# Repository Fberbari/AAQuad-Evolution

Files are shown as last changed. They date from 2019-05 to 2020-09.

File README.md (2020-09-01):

# AAQuad-Evolution
---

The AAQuad-Evolution is a flight computer I've designed to control a quadcopter. The computer takes care of continued stabilization in flight while leaving the pilot free to command roll, pitch, and yaw angles as well as altitude. The project is made up of a custom PCB, all the bare-metal C code that runs on the Atmega328pb processor and Matlab simulations used to design and tune the PID algorithms. This is very much a bare bones flight computer that is in no way as feature rich as BetaFlight or any of the other famous FOS flight controllers. Its advantage lies in its simplicity. Anyone with some understanding of the dynamics of flight, calculus, and circuitry could begin to understand the project without being faced with a mountain of complexity and no idea where to start. In the end, the AAQuad-Evolution continues to satisfy my curiosity for flight and increase my understanding of embedded systems all the while providing me with a creative outlet to try out all kinds of cool things.



## Flying the Quad
---

The commands are as such:

* Increasing/decreasing the throttle stick corresponds to an increase/decrease in the target altitude.
* Increasing/decreasing the rudder stick corresponds to an increase/decrease in the target azimuth (relative to the starting azimuth).
* Increasing/decreasing the aileron stick corresponds to an increase/decrease in the target bank angle.
* Increasing/decreasing the elevator stick corresponds to an increase/decrease in the target pitch angle.

The ranges for all the mentioned targets are defined in src/Pid.h.

## Calibrating the Quad
---

1. Before plugging in the battery, turn the transmitter on and put the throttle stick to full power.
2. Plug in the battery.
	* A solid green led will turn on, indicating calibration mode has been successfully entered.
3. Position the Quad on a level surface and make sure it is completely still.
4. Put the throttle stick to 0.
	* The led will turn off, indicating calibration has begun.
5. Once the led turns on again, the Quad has been successfully calibrated and is ready to be flown.

### Some in flight images

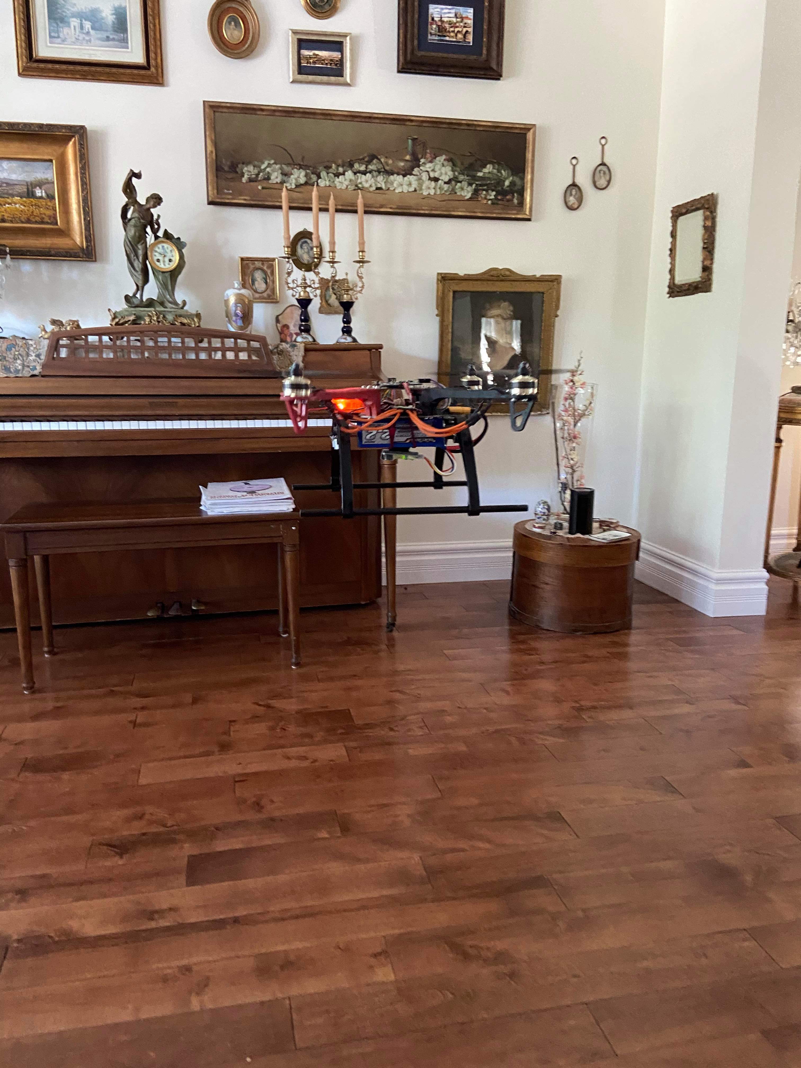
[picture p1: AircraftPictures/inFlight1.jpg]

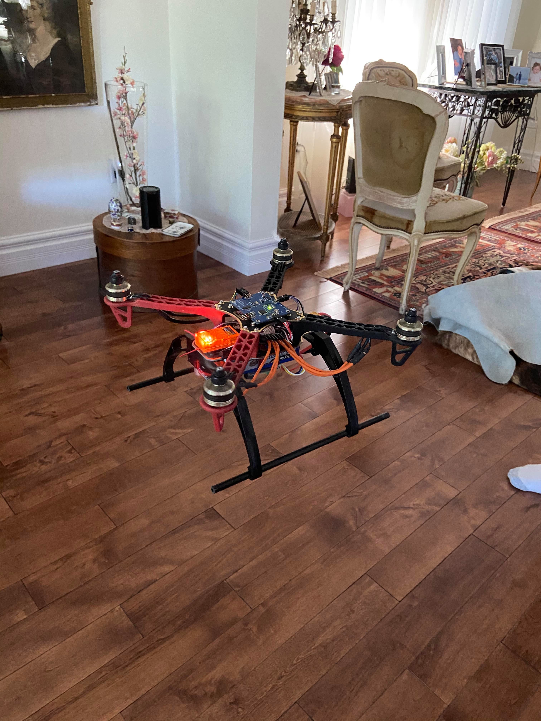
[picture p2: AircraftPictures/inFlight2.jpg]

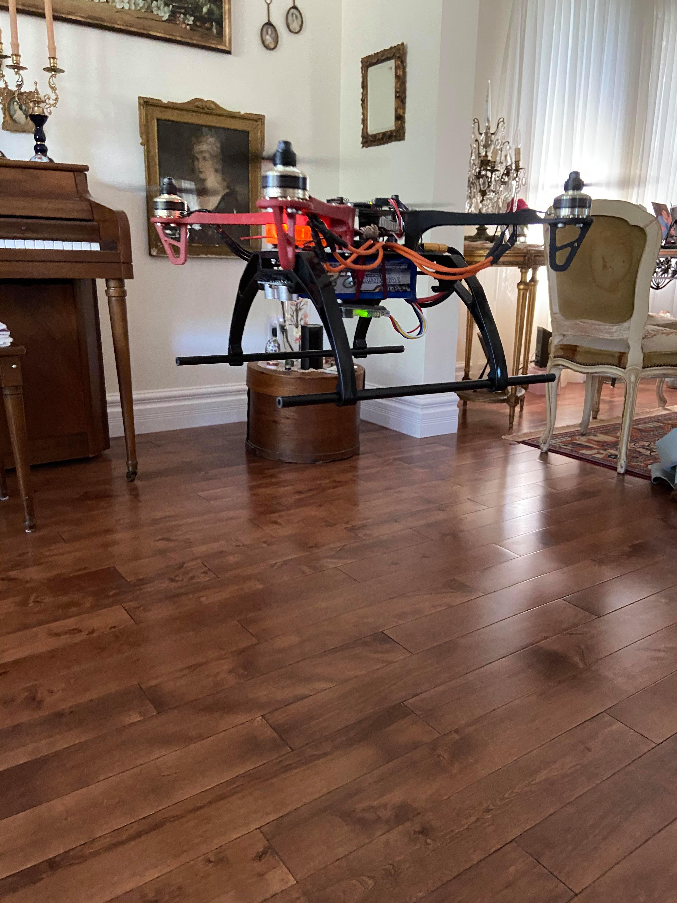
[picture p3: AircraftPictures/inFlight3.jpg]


### Some close ups

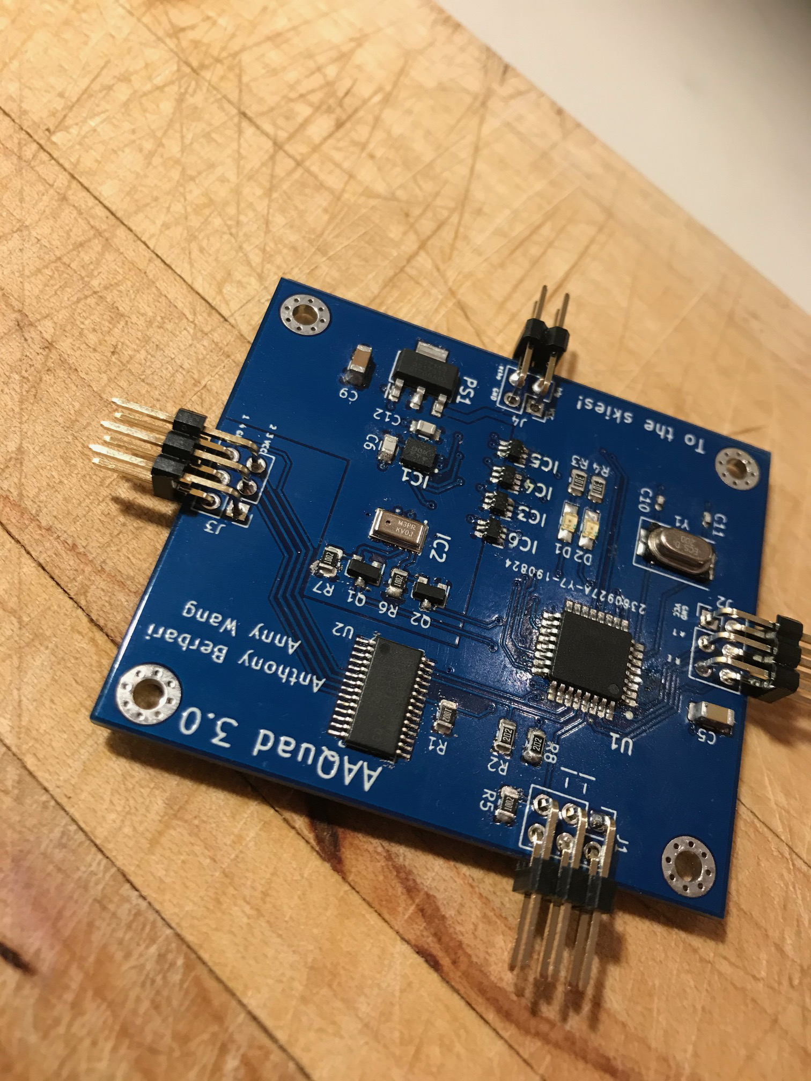
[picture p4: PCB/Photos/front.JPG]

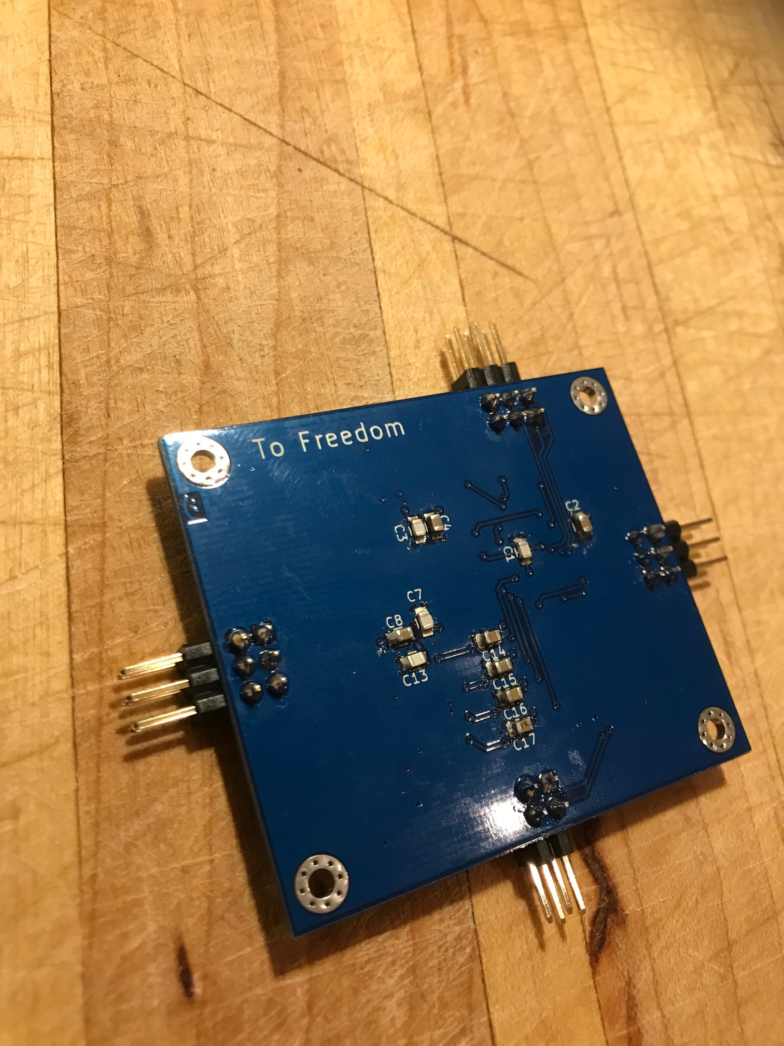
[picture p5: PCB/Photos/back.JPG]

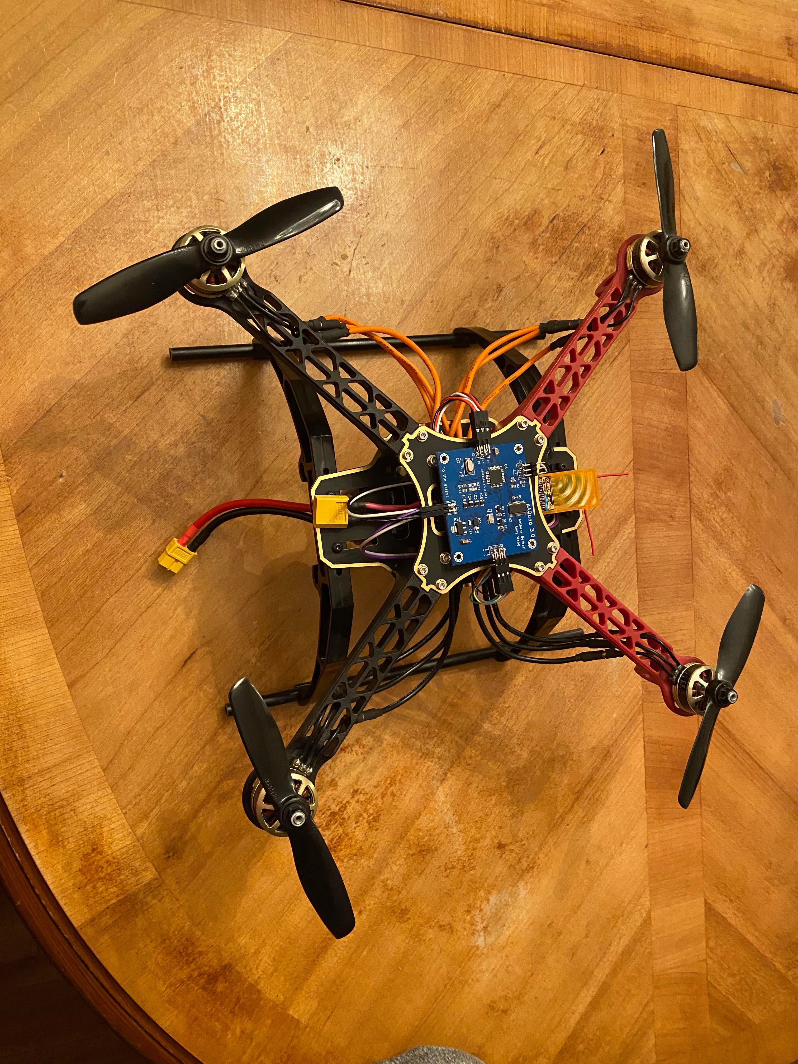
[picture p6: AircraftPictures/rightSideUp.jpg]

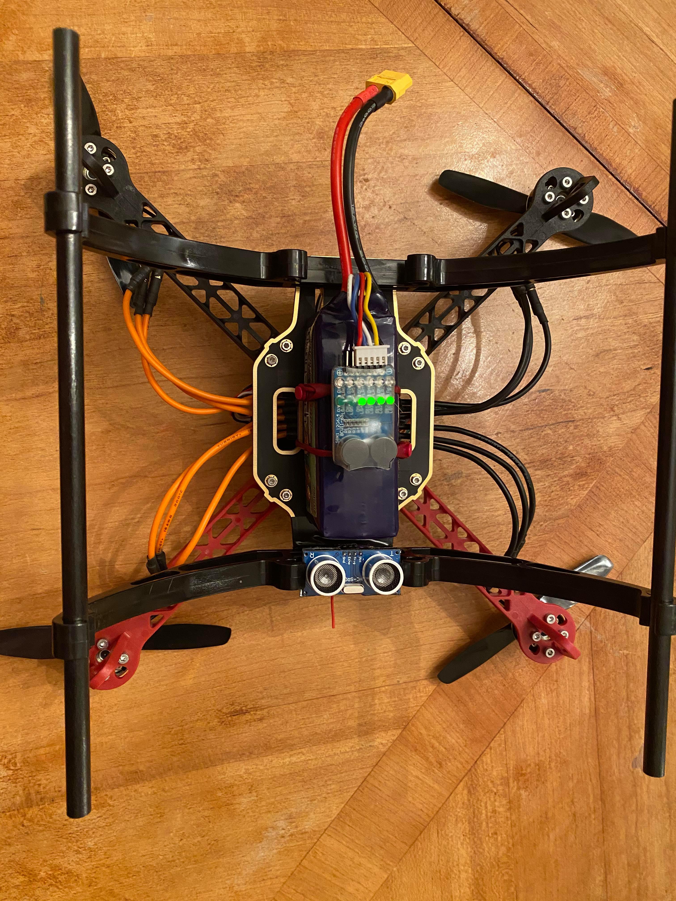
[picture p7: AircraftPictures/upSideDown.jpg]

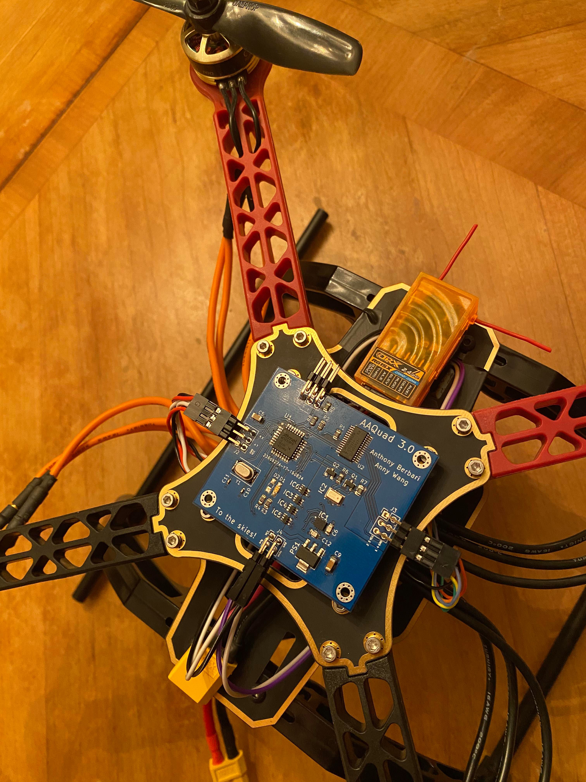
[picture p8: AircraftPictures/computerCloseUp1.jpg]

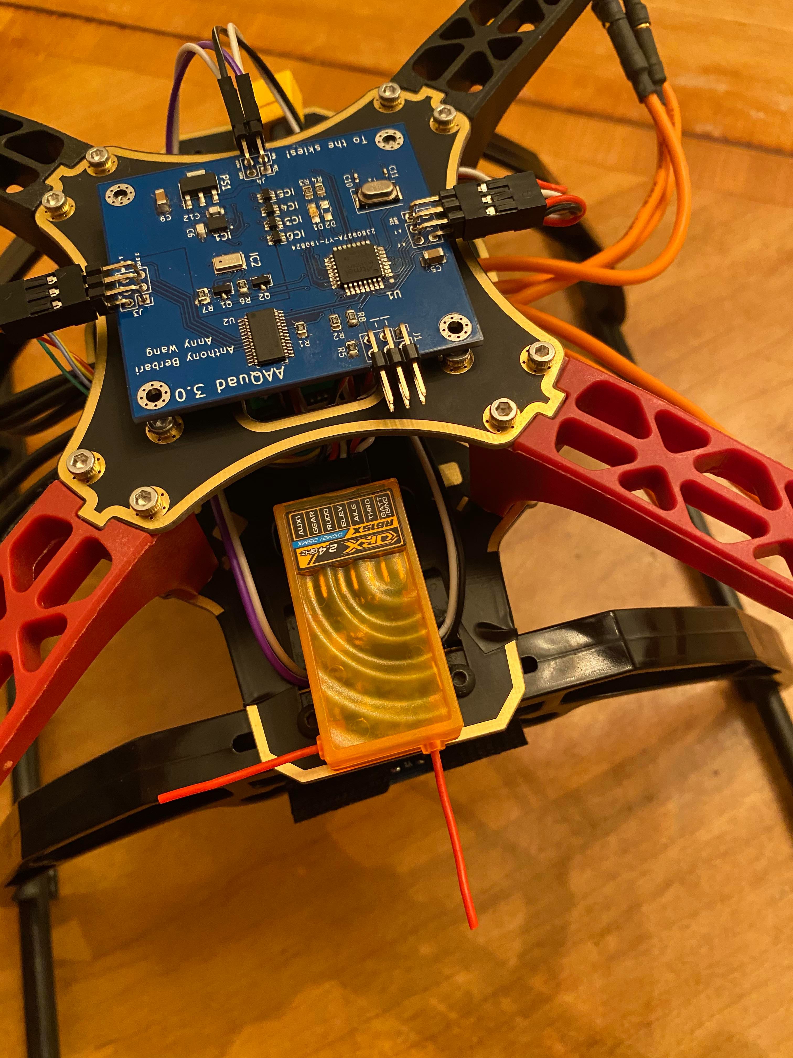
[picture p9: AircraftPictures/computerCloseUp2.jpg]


## What's going on ?
---

So you want to understand how the AAQuad flies ? Great! Here is a high level explanation of what's going on.

Everything starts in main.c, which you'll find in the root directory of the project. If you go through that file, you'll find it's incredibly simple in principle. Here, we begin with a short delay to ensure all electrical systems have stabilized after power up. Next, we execute a calibration and finally, we call the controller state machine inside an infinite loop (this is where the magic happens).

Now, let's head into the src directory. Apart from main.c, this is where all the the source and header files are stored. Take a look at the state machine in Controller.c (the switch case statement inside the Controller_DoYourThingAndFlyTheQuadITrustYou function). The switch statement is organized in the order that the states get executed. Here's what's going on:

1. GetPilotInstructions: We check to see whether there are any new instructions from the receiver. If you take a look inside the PilotInstructions module, you'll see that the pwm signals sent from the ESC are read asynchronously via external and pin change interrupts. Those instructions get translated into percentages for commanded roll, pitch, yaw and altitude. If they are ready when PilotInstructions_ComputePilotResult is called, we pick them up. Otherwise, we just move on and pick them up the next time.

2. GetImuData: We collect the accelerometer, gyroscope and magnetometer data from the inertial measurement unit. This is also an interrupt based exchanged so when we call Imu_GetResult, we are just checking if the data is ready and picking it up if it is.

3. GetAltitude: We collect data from the ultrasonic distance sensor. Once again, it is an interrupt based exchange, so we are just checking and picking data up if it is ready.

4. TriggerNewMeasurements: Now that we've collected all the data of interest, we need to instruct the sensors to collect more data for us. This way, when the time comes once again to ask for it, it will be ready. For the IMU, this triggers an interrupt based SPI exchange that reads the registers that contain the relevant data. For the ultrasonic distance sensor, this sends the digital pulse instructing it to collect a new measurement.

5. FuseMeasurements: While the sensors do their thing, we begin to crunch the math. In this state, we fuse gyroscope and accelerometer data together using a Mahony filter. This filter returns the estimated orientation of the quad encoded in a quaternion.

6. ConvertToEuler: Since quaternions are very non linear and thus hard to use in a linear controller, we convert them into Euler angles. These are the familiar roll, pitch and yaw angles. At the same time, we also compute the derivatives of the Euler angles (representative of the angular velocity of the quad in every axis). This is for future use in the controller. It is done this way because computing a derivative from the change in measured angular positions leaves us very susceptible to noise. Since we have a gyroscope and measure the derivatives directly, we can use those values and avoid this problem.

7. ComputePid: Now that we know what the pilot wants and what the quad is doing, we can compute what we need the motors to do to achieve the pilot's intentions. This is done via multiple PID (proportional, integral, derivative) algorithms. This module also takes care of figuring out the takeoff sequence of the quad. What we get from it is an array of 4 floats that correspond to percentages of full power that need to be delivered to each motor to achieve the desired intentions.

8. SendToPwm: Once we know what we want the motors to do, we need to communicate that to them. To do so, we begin an interrupt based I2C exchange with a chip responsible for sending out PWM to the ESC.

9. WaitForTimer: Last, to keep things synchronous, we sit in this state until a timer says some set time has passed. Once that is the case, we go back to the GetPilotInstructions state and the cycle begins anew.

10. Failed: This state should never be reached in normal flight but exists in case a catastrophic failure needs to be handled. In the case that something goes horribly wrong in one of the modules (for example communication gets cut with one of our chips), we go to this state and the PWM output to the ESC gets immediately shutdown, causing the motors to stop spinning.

## Building it for yourself
---

A word of caution. This project was not designed to be reproduced, so it is fairly difficult to do so. That being said, if anyone does want to construct the PCB and tune then upload the software, here is what they would need to do:

### Prereq Hardware

* [Avr-Ice Jtag programmer](https://www.digikey.ca/en/product-highlight/a/atmel/atmel-ice-programmer-debugger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)
* A 4 channel ESC with 5V BEC that can handle 200 Hz PWM refresh rates
* A minimum 4 channel receiver that communicates over PWM
* Your favorite quadcopter frame, motors, and battery
* A transmitter capable of communicating with your esc of choice

### Prereq Software

* Atmel studio 7+
* Kicad 5+ (Optional, as the gerbers are already in the repo)
* Simulink 2019+, equipped with the aerospace blockset

### Building the PCB

Full gerber files and a BOM are present in the PCB/KicadFiles directory.
The only sensor not present in the BOM is the [ultrasonic distance sensor](https://www.sparkfun.com/products/15569).
You will also need to purchase the appropriate wires to connect the ESC, receiver, and ultrasonic sensor to the PCB.

### Adjusting the PID gains

If you know the mass, inertia tensor, and relationship between throttle percentage, force and torque of your quadcopter, you can adjust the appropriate blocks in the Simulink model and tune the PID gains. You can insert those gains into src/Pid.c.

### Compiling and uploading the software

Once the pcb is built, power it by connecting the ESC to the battery and plug in the Jtag programmer to the appropriate pins. To open the project in Atmel studio, open the project file present in /build. Then, click the compile button and the run button.

## License

This project is under the MIT license.

## Acknowledgements

* SOH Madgwick, whose implementation of the Mahony filter is used in this project.
* A shoutout to Anny Wang, who said: "Hey, wouldn't it be cool to build a quadcopter ?" back in 2018, which is how this project began :p.

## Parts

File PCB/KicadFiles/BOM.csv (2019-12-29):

value | footprint | libsource/_lib | libsource/_part | libsource/_description | sheetpath/_names | sheetpath/_tstamps | tstamp | _ref | datasheet | fields/field/0/_name | fields/field/0/__text | fields/field/1/_name | fields/field/1/__text | fields/field/2/_name | fields/field/2/__text | fields/field/3/_name | fields/field/3/__text | fields/field/4/_name | fields/field/4/__text | fields/field/5/_name | fields/field/5/__text | fields/field/6/_name | fields/field/6/__text | fields/field/7/_name | fields/field/7/__text | fields/field/8/_name | fields/field/8/__text
programmer | Connector_PinHeader_2.54mm:PinHeader_2x03_P2.54mm_Vertical | AAquad_PCB-rescue | Conn_02x03_Counter_Clockwise |  | / | / | 5AFFD18C | J1
10K | Resistor_SMD:R_0805_2012Metric | AAquad_PCB-rescue | R |  | / | / | 5B009C4D | R6
0.1uF | Capacitors_SMD:C_0805 | AAquad_PCB-rescue | C |  | / | / | 5B01389E | C7
10uF | Capacitors_SMD:C_0805 | AAquad_PCB-rescue | C |  | / | / | 5B01393C | C8
green | LEDs:LED_0805_HandSoldering | AAquad_PCB-rescue | LED |  | / | / | 5B01445F | D1
0.1uF | Capacitors_SMD:C_0805 | AAquad_PCB-rescue | C |  | / | / | 5B01AE0E | C3
10uF | Capacitors_SMD:C_0805 | AAquad_PCB-rescue | C |  | / | / | 5B01AECE | C4
0.1uF | Capacitors_SMD:C_0805 | AAquad_PCB-rescue | C |  | / | / | 5B01F518 | C1
10uF | Capacitors_SMD:C_0805 | AAquad_PCB-rescue | C |  | / | / | 5B01F5DD | C2
10K | Resistor_SMD:R_0805_2012Metric | AAquad_PCB-rescue | R |  | / | / | 5B020FB2 | R5
300 | Resistor_SMD:R_0805_2012Metric | AAquad_PCB-rescue | R |  | / | / | 5B014D38 | R3
BSS138 | TO_SOT_Packages_SMD:SOT-23 | AAquad_PCB-rescue | BSS138 |  | / | / | 5B066D86 | Q2
BSS138 | TO_SOT_Packages_SMD:SOT-23 | AAquad_PCB-rescue | BSS138 |  | / | / | 5B0670F5 | Q1
SPX1117M3-L-5-0_TR | SamacSys_Parts:SOT230P700X170-4N | AAquad_PCB-rescue | SPX1117M3-L-5-0_TR |  | / | / | 5B6A5D1A | PS1 | https://www.exar.com/ds/spx1117_ds_r210_082411.pdf | Arrow Part Number | SPX1117M3-L-5-0/TR | Arrow Price/Stock | https://www.arrow.com/en/products/spx1117m3-l-5-0tr/exar | Description | LDO Voltage Regulators 800mALOW DROPOUT | Height | 1.7 | Manufacturer_Name | EXAR | Manufacturer_Part_Number | SPX1117M3-L-5-0/TR
MPL3115A2 | sensors:MPL3115A2 | MPL3115A2 | MPL3115A2 | MPL3115A2, Absolute Pressure Sensor, 110kPa 0.9 1 V Output, 8-Pin LGA | / | / | 5D61CB39 | IC2 | http://uk.rs-online.com/web/p/products/7500841 | Description | MPL3115A2, Absolute Pressure Sensor, 110kPa 0.9 1 V Output, 8-Pin LGA | Manufacturer_Name | Nexperia | Manufacturer_Part_Number | MPL3115A2 | RS Part Number | 7500841 | RS Price/Stock | http://uk.rs-online.com/web/p/products/7500841
0.1uF | Capacitors_SMD:C_0805 | Device | C | Unpolarized capacitor | / | / | 5D72BD62 | C13 | ~
100uF | Capacitor_SMD:C_1206_3216Metric | Device | C | Unpolarized capacitor | / | / | 5DA2FA31 | C9 | ~
BMX160 | sensors:bmx160 | BMX160 | BMX160 | IMUs - Inertial Measurement Units 9-axis (9DOF) Absolute Orientation MEMS Sensor | / | / | 5DA63717 | IC1 | http://www.mouser.com/datasheet/2/783/BST-BMX160-DS000-11-1480547.pdf | Description | IMUs - Inertial Measurement Units 9-axis (9DOF) Absolute Orientation MEMS Sensor | Height | 0.88 | Manufacturer_Name | Bosch Sensortec | Manufacturer_Part_Number | BMX160 | Mouser Part Number | 262-BMX160 | Mouser Price/Stock | https://www.mouser.com/Search/Refine.aspx?Keyword=262-BMX160
10K | Resistor_SMD:R_0805_2012Metric | Device | R | Resistor | / | / | 5DCD5F56 | R1 | ~
PCA9685PW_112 | digikey-footprints:TSSOP-28_W4.40mm | AAquad_PCB-rescue | PCA9685PW_112-RESCUE-AAquad_PCB |  | / | / | 5B007CE9 | U2 | https://www.nxp.com/docs/en/data-sheet/PCA9685.pdf | Category | Integrated Circuits (ICs) | DK_Datasheet_Link | https://www.nxp.com/docs/en/data-sheet/PCA9685.pdf | DK_Detail_Page | /product-detail/en/nxp-usa-inc/PCA9685PW,112/568-8366-5-ND/2034324 | Description | IC LED DRVR LIN DIM 25MA 28TSSOP | Digi-Key_PN | 568-8366-5-ND | Family | PMIC - LED Drivers | MPN | PCA9685PW,112 | Manufacturer | NXP USA Inc. | Status | Active
2K | Resistor_SMD:R_0805_2012Metric | Device | R | Resistor | / | / | 5DE25B41 | R8 | ~
2K | Resistor_SMD:R_0805_2012Metric | Device | R | Resistor | / | / | 5DE26598 | R2 | ~
Atmega328pb | microcontrollers:ATMEGA328PB-ANR | Misc | Atmega328pb |  | / | / | 5D60BAF7 | U1
10K | Resistor_SMD:R_0805_2012Metric | AAquad_PCB-rescue | R |  | / | / | 5B009BD8 | R7
Crystal | Crystals:Crystal_SMD_7050-2pin_7.0x5.0mm | Device | Crystal | Two pin crystal | / | / | 5D83D52A | Y1 | ~
33pF | Capacitor_SMD:C_0402_1005Metric | Device | C | Unpolarized capacitor | / | / | 5D880116 | C11 | ~
33pF | Capacitor_SMD:C_0402_1005Metric | Device | C | Unpolarized capacitor | / | / | 5D88142F | C10 | ~
Receiver_Output | Connector_PinHeader_2.54mm:PinHeader_2x03_P2.54mm_Vertical | Connector_Generic | Conn_02x03_Counter_Clockwise | Generic connector, double row, 02x03, counter clockwise pin numbering scheme (similar to DIP packge numbering), script generated (kicad-library-utils/schlib/autogen/connector/) | / | / | 5D8ADF89 | J2 | ~
ESC_Input | Connector_PinHeader_2.54mm:PinHeader_2x03_P2.54mm_Vertical | Connector_Generic | Conn_02x03_Counter_Clockwise | Generic connector, double row, 02x03, counter clockwise pin numbering scheme (similar to DIP packge numbering), script generated (kicad-library-utils/schlib/autogen/connector/) | / | / | 5D8AF12E | J3 | ~
100uF | Capacitor_SMD:C_1206_3216Metric | Device | C | Unpolarized capacitor | / | / | 5D990D4F | C5 | ~
0.1uF | Capacitors_SMD:C_0805 | Device | C | Unpolarized capacitor | / | / | 5D9AE831 | C6 | ~
0.1uF | Capacitors_SMD:C_0805 | Device | C | Unpolarized capacitor | / | / | 5D9BB021 | C12 | ~
300 | Resistor_SMD:R_0805_2012Metric | AAquad_PCB-rescue | R |  | / | / | 5B014C86 | R4
red | LEDs:LED_0805_HandSoldering | AAquad_PCB-rescue | LED |  | / | / | 5B014543 | D2
ultrasonic | Connector_PinHeader_2.54mm:PinHeader_2x02_P2.54mm_Vertical | Connector_Generic | Conn_02x02_Counter_Clockwise | Generic connector, double row, 02x02, counter clockwise pin numbering scheme (similar to DIP packge numbering), script generated (kicad-library-utils/schlib/autogen/connector/) | / | / | 5DA7B7E2 | J4 | ~
levelShifter | levelShifters:74LVC1T45GW_125 | 74LVC1T45GW_125 | 74LVC1T45GW,125 | NXP - 74LVC1T45GW,125 - TRANSCEIVER, 3 STATE, SOT-363-6 | / | / | 5DB12994 | IC3 | https://componentsearchengine.com/Datasheets/1/74LVC1T45GW,125.pdf | Description | NXP - 74LVC1T45GW,125 - TRANSCEIVER, 3 STATE, SOT-363-6 | Height | 1.1 | Manufacturer_Name | Nexperia | Manufacturer_Part_Number | 74LVC1T45GW,125 | Mouser Part Number | 771-74LVC1T45GW125 | Mouser Price/Stock | https://www.mouser.com/Search/Refine.aspx?Keyword=771-74LVC1T45GW125
levelShifter | levelShifters:74LVC1T45GW_125 | 74LVC1T45GW_125 | 74LVC1T45GW,125 | NXP - 74LVC1T45GW,125 - TRANSCEIVER, 3 STATE, SOT-363-6 | / | / | 5DB795A6 | IC4 | https://componentsearchengine.com/Datasheets/1/74LVC1T45GW,125.pdf | Description | NXP - 74LVC1T45GW,125 - TRANSCEIVER, 3 STATE, SOT-363-6 | Height | 1.1 | Manufacturer_Name | Nexperia | Manufacturer_Part_Number | 74LVC1T45GW,125 | Mouser Part Number | 771-74LVC1T45GW125 | Mouser Price/Stock | https://www.mouser.com/Search/Refine.aspx?Keyword=771-74LVC1T45GW125
levelShifter | levelShifters:74LVC1T45GW_125 | 74LVC1T45GW_125 | 74LVC1T45GW,125 | NXP - 74LVC1T45GW,125 - TRANSCEIVER, 3 STATE, SOT-363-6 | / | / | 5DB8B8A0 | IC5 | https://componentsearchengine.com/Datasheets/1/74LVC1T45GW,125.pdf | Description | NXP - 74LVC1T45GW,125 - TRANSCEIVER, 3 STATE, SOT-363-6 | Height | 1.1 | Manufacturer_Name | Nexperia | Manufacturer_Part_Number | 74LVC1T45GW,125 | Mouser Part Number | 771-74LVC1T45GW125 | Mouser Price/Stock | https://www.mouser.com/Search/Refine.aspx?Keyword=771-74LVC1T45GW125
levelShifter | levelShifters:74LVC1T45GW_125 | 74LVC1T45GW_125 | 74LVC1T45GW,125 | NXP - 74LVC1T45GW,125 - TRANSCEIVER, 3 STATE, SOT-363-6 | / | / | 5DBA6F7E | IC6 | https://componentsearchengine.com/Datasheets/1/74LVC1T45GW,125.pdf | Description | NXP - 74LVC1T45GW,125 - TRANSCEIVER, 3 STATE, SOT-363-6 | Height | 1.1 | Manufacturer_Name | Nexperia | Manufacturer_Part_Number | 74LVC1T45GW,125 | Mouser Part Number | 771-74LVC1T45GW125 | Mouser Price/Stock | https://www.mouser.com/Search/Refine.aspx?Keyword=771-74LVC1T45GW125
10uF | Capacitor_SMD:C_0805_2012Metric | Device | C | Unpolarized capacitor | / | / | 5DBEEB7C | C14 | ~
10uF | Capacitor_SMD:C_0805_2012Metric | Device | C | Unpolarized capacitor | / | / | 5DBEF6BD | C15 | ~
10uF | Capacitor_SMD:C_0805_2012Metric | Device | C | Unpolarized capacitor | / | / | 5DBEFEA3 | C16 | ~
10uF | Capacitor_SMD:C_0805_2012Metric | Device | C | Unpolarized capacitor | / | / | 5DBF0B0D | C17 | ~

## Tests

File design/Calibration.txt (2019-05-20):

tests:

	1. If pilot does not raise throttle, calibration is not saved. 				P
	2. if pilot raises throttle, go to try saving calibration.					P
	3. Wait until Pilot Lowers Throttle.										P
	3. In saving a calibration, correct data is gathered from the sensors.		P
	4. It is written to eeprom.													P
	5. In loading calibration, correct data is gathered from eeprom.			P
	6. In loading calibration, correct dta is written to the module.			P

Caveats:
	1. It is quite possible that the very first pilot reading is the one used. does this work ?		P

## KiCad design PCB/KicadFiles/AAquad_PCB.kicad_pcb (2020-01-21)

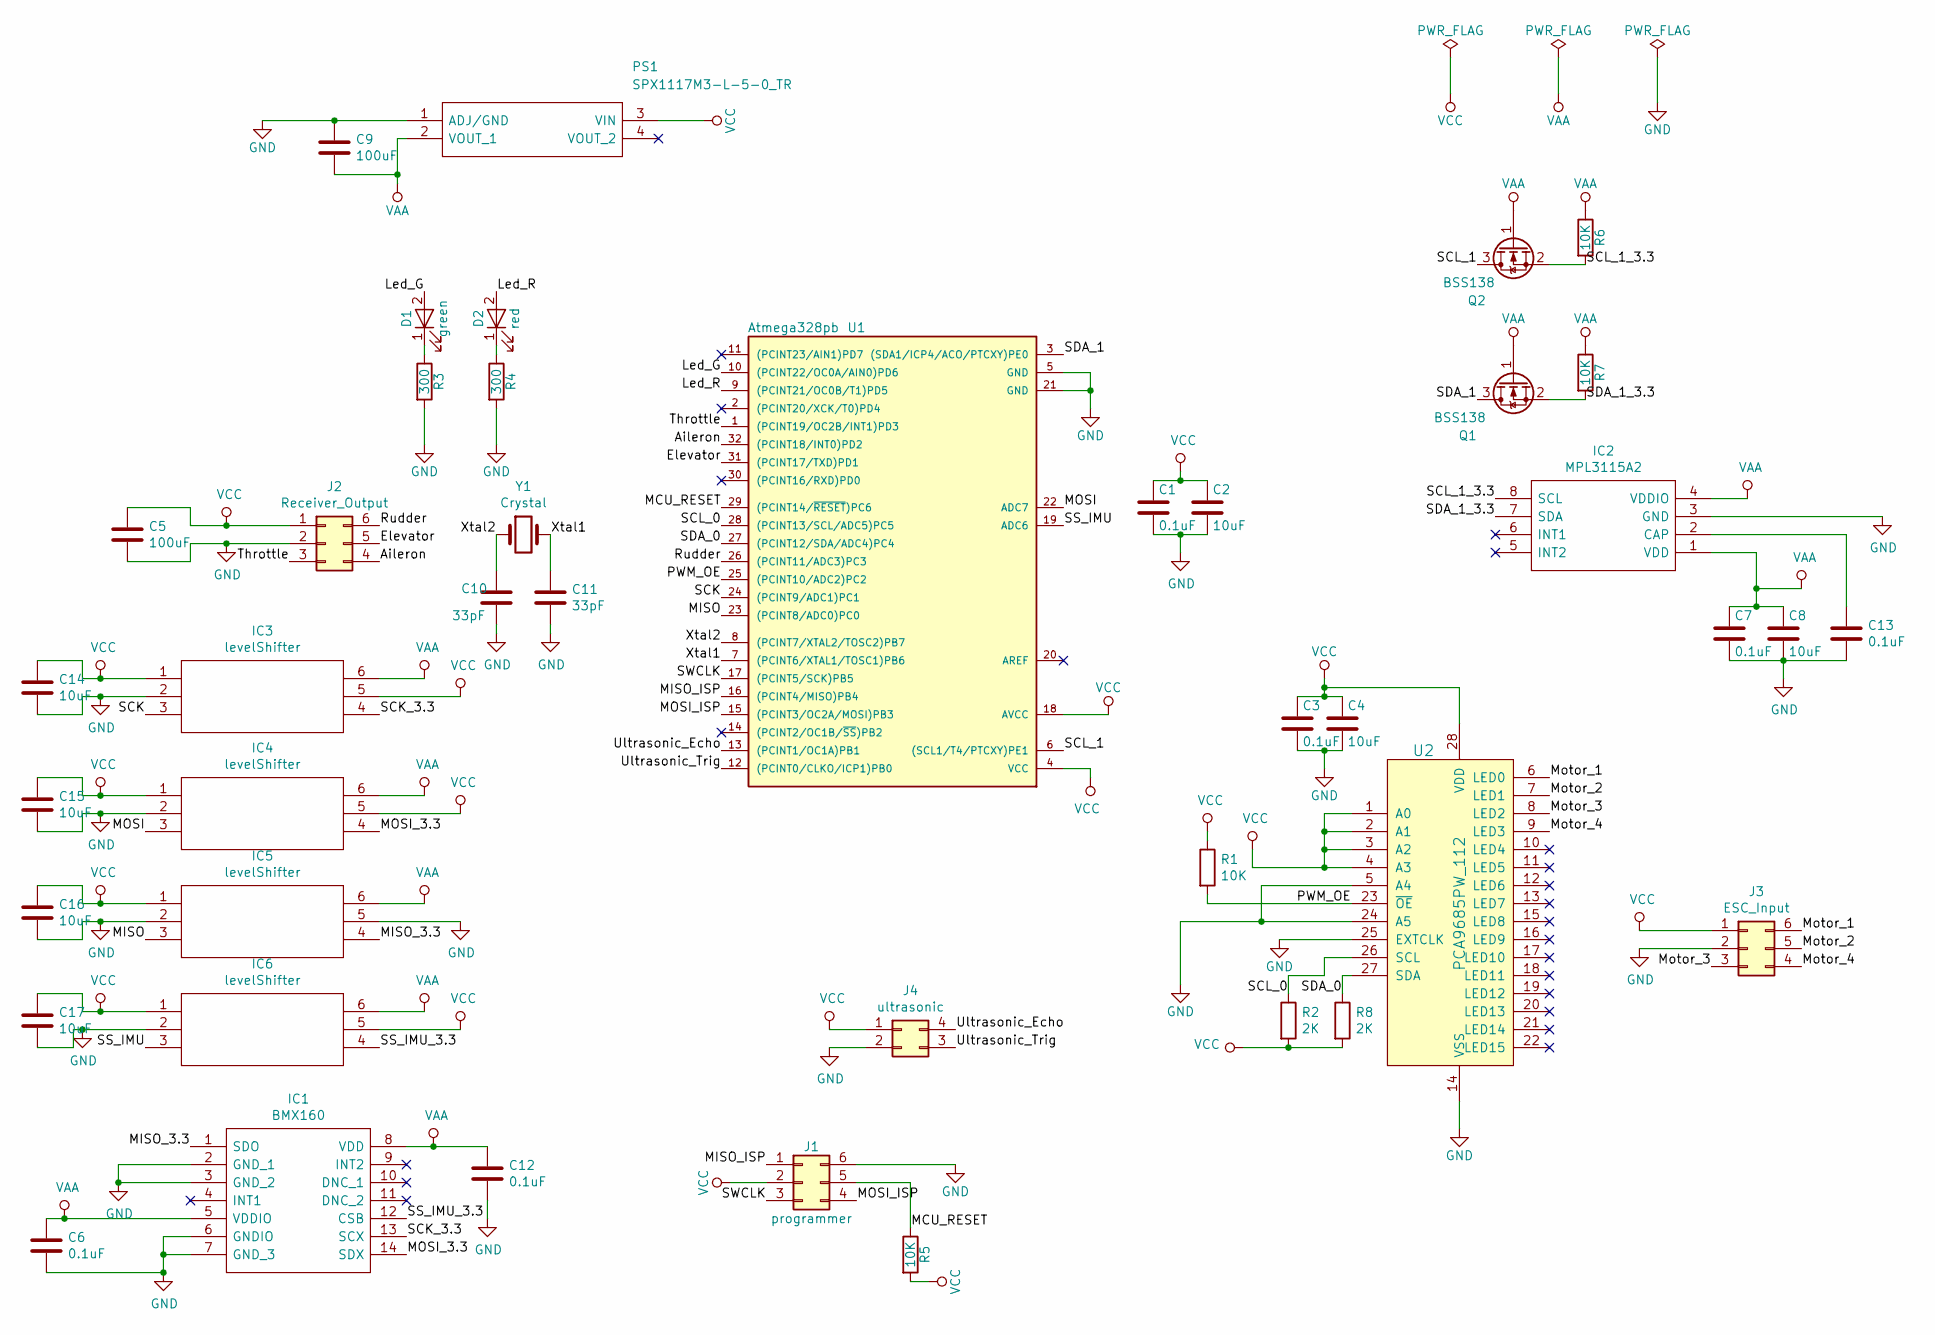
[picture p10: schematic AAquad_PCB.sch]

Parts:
C1, C3, C6, C7, C12, C13: 0.1uF; C_0805
C2, C4, C8: 10uF; C_0805
C5, C9: 100uF; C_1206_3216Metric
C10, C11: 33pF; C_0402_1005Metric
C14, C15, C16, C17: 10uF; C_0805_2012Metric
D1: green; LED_0805_HandSoldering
D2: red; LED_0805_HandSoldering
IC1: BMX160; bmx160; Manufacturer_Part_Number BMX160; Mouser Part Number 262-BMX160
IC2: MPL3115A2; Manufacturer_Part_Number MPL3115A2
IC3, IC4, IC5, IC6: levelShifter; 74LVC1T45GW_125; Mouser Part Number 771-74LVC1T45GW125
J1: programmer; PinHeader_2x03_P2.54mm_Vertical
J2: Receiver_Output; PinHeader_2x03_P2.54mm_Vertical
J3: ESC_Input; PinHeader_2x03_P2.54mm_Vertical
J4: ultrasonic; PinHeader_2x02_P2.54mm_Vertical
PS1: SPX1117M3-L-5-0_TR; SOT230P700X170-4N; Manufacturer_Part_Number SPX1117M3-L-5-0/TR
Q1, Q2: BSS138; SOT-23
R1, R5, R6, R7: 10K; R_0805_2012Metric
R2, R8: 2K; R_0805_2012Metric
R3, R4: 300; R_0805_2012Metric
U1: Atmega328pb; ATMEGA328PB-ANR
U2: PCA9685PW_112; TSSOP-28_W4.40mm; MPN PCA9685PW,112; Digi-Key_PN 568-8366-5-ND
Y1: Crystal; Crystal_SMD_7050-2pin_7.0x5.0mm

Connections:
/Aileron: J2.4, U1.32 ((PCINT18/INT0)PD2)
/Elevator: J2.5, U1.31 ((PCINT17/TXD)PD1)
/Led_G: D1.2 (A), U1.10 ((PCINT22/OC0A/AIN0)PD6)
/Led_R: D2.2 (A), U1.9 ((PCINT21/OC0B/T1)PD5)
/MCU_RESET: J1.5, R5.1, U1.29 ((PCINT14/~RESET~)PC6)
/MISO: IC5.3, U1.23 ((PCINT8/ADC0)PC0)
/MISO_3.3: IC1.1 (SDO), IC5.4
/MISO_ISP: J1.1, U1.16 ((PCINT4/MISO)PB4)
/MOSI: IC4.3, U1.22 (ADC7)
/MOSI_3.3: IC1.14 (SDX), IC4.4
/MOSI_ISP: J1.4, U1.15 ((PCINT3/OC2A/MOSI)PB3)
/Motor_1: J3.6, U2.6 (LED0)
/Motor_2: J3.5, U2.7 (LED1)
/Motor_3: J3.3, U2.8 (LED2)
/Motor_4: J3.4, U2.9 (LED3)
/PWM_OE: R1.2, U1.25 ((PCINT10/ADC2)PC2), U2.23 (~OE)
/Rudder: J2.6, U1.26 ((PCINT11/ADC3)PC3)
/SCK: IC3.3, U1.24 ((PCINT9/ADC1)PC1)
/SCK_3.3: IC1.13 (SCX), IC3.4
/SCL_0: R2.1, U1.28 ((PCINT13/SCL/ADC5)PC5), U2.26 (SCL)
/SCL_1: Q2.3 (D), U1.6 ((SCL1/T4/PTCXY)PE1)
/SCL_1_3.3: IC2.8 (SCL), Q2.2 (S), R6.2
/SDA_0: R8.1, U1.27 ((PCINT12/SDA/ADC4)PC4), U2.27 (SDA)
/SDA_1: Q1.3 (D), U1.3 ((SDA1/ICP4/ACO/PTCXY)PE0)
/SDA_1_3.3: IC2.7 (SDA), Q1.2 (S), R7.2
/SS_IMU: IC6.3, U1.19 (ADC6)
/SS_IMU_3.3: IC1.12 (CSB), IC6.4
/SWCLK: J1.3, U1.17 ((PCINT5/SCK)PB5)
/Throttle: J2.3, U1.1 ((PCINT19/OC2B/INT1)PD3)
/Ultrasonic_Echo: J4.4, U1.13 ((PCINT1/OC1A)PB1)
/Ultrasonic_Trig: J4.3, U1.12 ((PCINT0/CLKO/ICP1)PB0)
/Xtal1: C11.1, U1.7 ((PCINT6/XTAL1/TOSC1)PB6), Y1.2
/Xtal2: C10.1, U1.8 ((PCINT7/XTAL2/TOSC2)PB7), Y1.1
GND: C1.2, C2.2, C3.2, C4.2, C5.2, C6.1, C7.2, C8.2, C9.1, C10.2, C11.2, C12.1, C13.2, C14.2, C15.2, C16.2, C17.2, IC1.2 (GND_1), IC1.3 (GND_2), IC1.6 (GNDIO), IC1.7 (GND_3), IC2.3 (GND), IC3.2, IC4.2, IC5.2, IC5.5, IC6.2, J1.6, J2.2, J3.2, J4.2, PS1.1 (ADJ/GND), R3.2, R4.2, U1.5 (GND), U1.21 (GND), U2.5 (A4), U2.14 (VSS), U2.24 (A5), U2.25 (EXTCLK)
unnamed: C13.1, IC2.2 (CAP)
unnamed: D1.1 (K), R3.1
unnamed: D2.1 (K), R4.1
VAA: C6.2, C7.1, C8.1, C9.2, C12.2, IC1.5 (VDDIO), IC1.8 (VDD), IC2.1 (VDD), IC2.4 (VDDIO), IC3.6, IC4.6, IC5.6, IC6.6, PS1.2 (VOUT_1), Q1.1 (G), Q2.1 (G), R6.1, R7.1
VCC: C1.1, C2.1, C3.1, C4.1, C5.1, C14.1, C15.1, C16.1, C17.1, IC3.1, IC3.5, IC4.1, IC4.5, IC5.1, IC6.1, IC6.5, J1.2, J2.1, J3.1, J4.1, PS1.3 (VIN), R1.1, R2.2, R5.2, R8.2, U1.4 (VCC), U1.18 (AVCC), U2.1 (A0), U2.2 (A1), U2.3 (A2), U2.4 (A3), U2.28 (VDD)

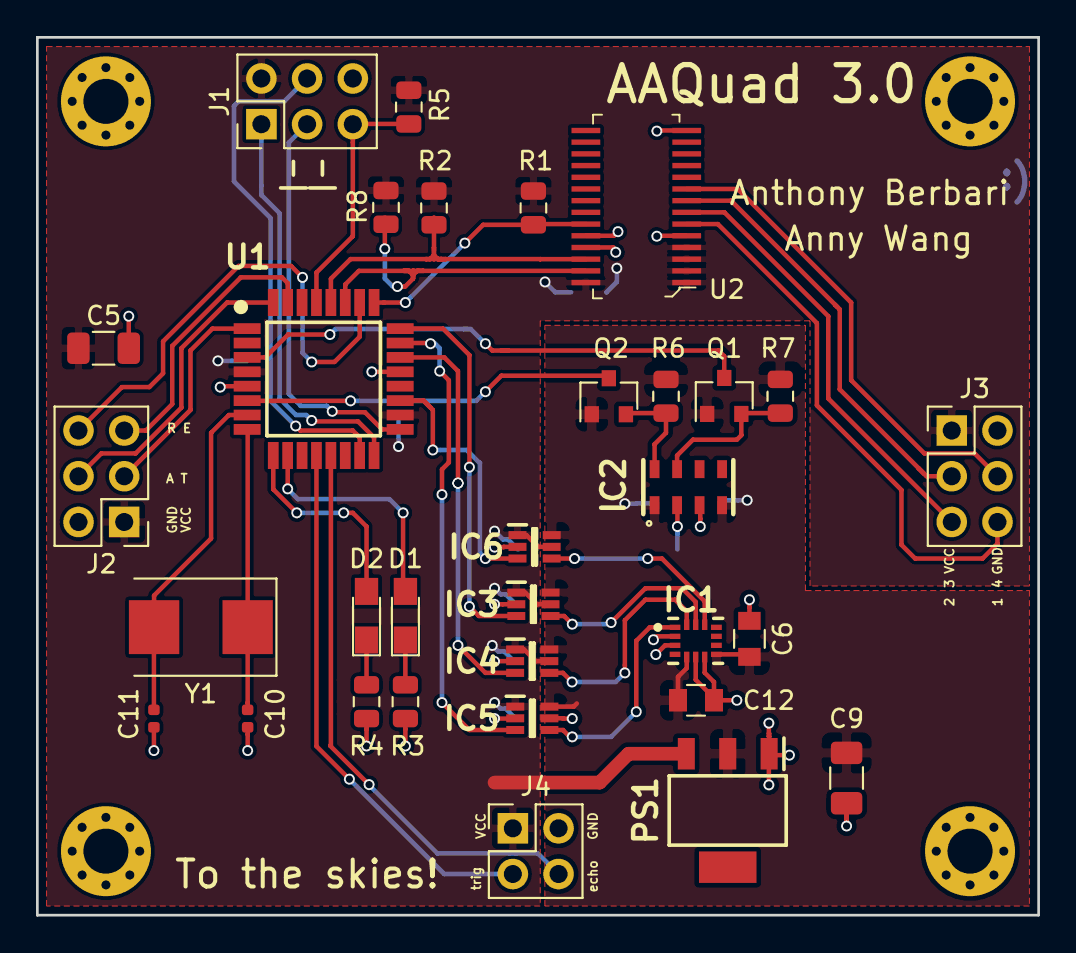
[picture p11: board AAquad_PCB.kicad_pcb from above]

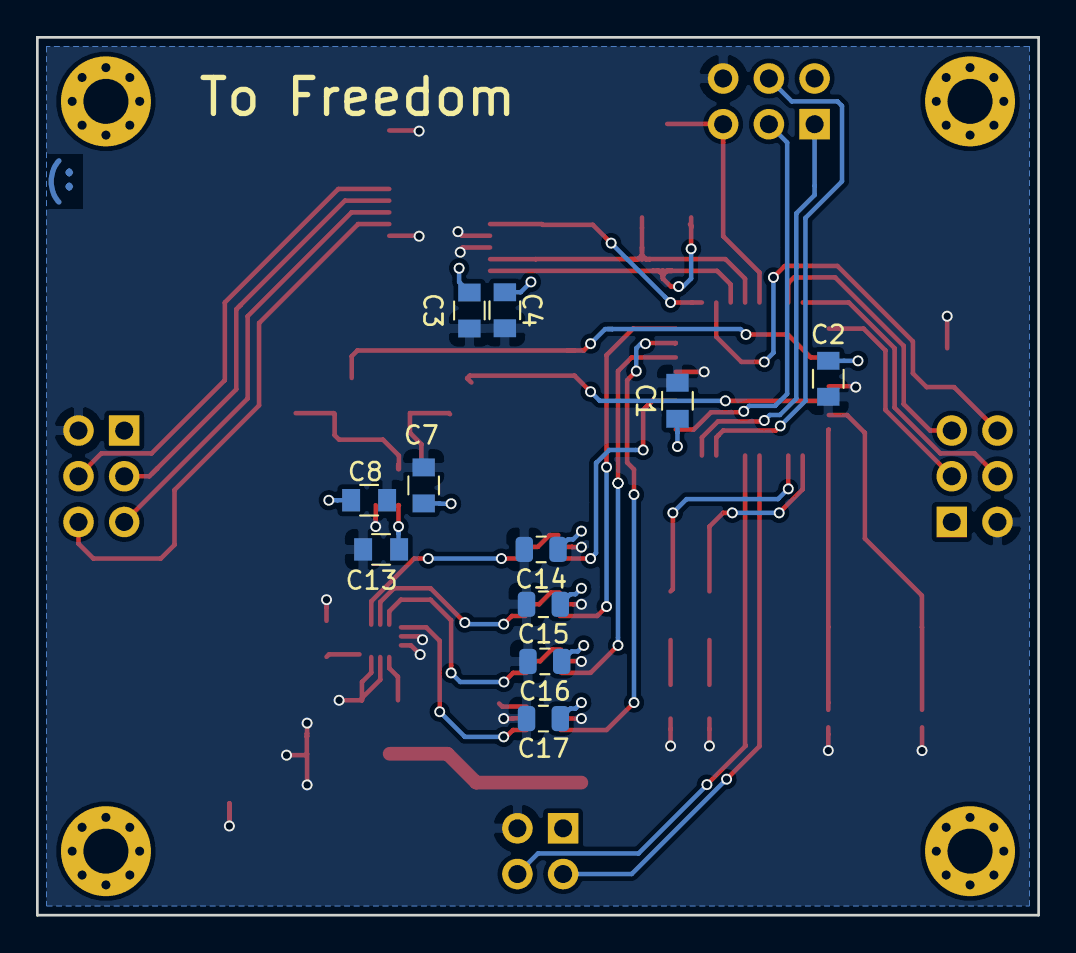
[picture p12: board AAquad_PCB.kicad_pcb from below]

Board: 2 copper layers, 55.6 x 48.8 mm, 43 parts (11 on the bottom side), 39 nets.

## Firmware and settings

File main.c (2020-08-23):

/*
 * AAQuad-Evolution
 *
 * Firmware Developer : Anthony Berbari
 */

#include "Controller.h"
#include "Calibration.h"

#include "Common.h"

/***********************************************************************************************************************
 * Definitions
 **********************************************************************************************************************/

#define TIME_TO_SETTLE_MS 500

/***********************************************************************************************************************
 * Code
 **********************************************************************************************************************/

int main(void)
{
    _delay_ms(TIME_TO_SETTLE_MS);

	Controller_Init();
    Calibration_Calibrate();

    while (1)
    {
    	Controller_DoYourThingAndFlyTheQuadITrustYou();
    }

}

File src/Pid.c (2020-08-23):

#include "Pid.h"

/***********************************************************************************************************************
 * Definitions
 **********************************************************************************************************************/

#define kpX 20.0f
#define kdX 2.0f
#define kiX 1.0f

#define kpY 20.0f
#define kdY 2.0f
#define kiY 1.0f

#define kpZ 20.0f
#define kdZ 2.0f
#define kiZ 1.0f

#define kpA 15.0f
#define kdA 30.0f
#define kiA 1.0f

#define TS CTRL_LOOP_PERIOD

#define TSA ALTITUDE_REFRESH_PERIOD

/***********************************************************************************************************************
 * Variables
 **********************************************************************************************************************/

static float xAccumulatedIntegral;
static float yAccumulatedIntegral;
static float zAccumulatedIntegral;
static float altitudeAccumulatedIntegral;

static float historicalAltitudeValue[3];

static float softStartMotorPercent;
static bool inFLight;

/***********************************************************************************************************************
 * Prototypes
 **********************************************************************************************************************/

static float ComputeHeadingPid(float desired, float actual, float actualRate, float kp, float ki, float kd, float *accumulatedIntegral);
static float ComputeZPid(float desired, float actual, float actualRate);
static float ComputeAltitudePid(float desired, float actual, EulerZYX_t *EulerAngles);
static void ConstrainMotorRanges(float *motors);

/***********************************************************************************************************************
 * Code
 **********************************************************************************************************************/

void Pid_Init(void)
{
    softStartMotorPercent = 0.0f;
    inFLight = false;
}

int Pid_Compute(PilotResult_t *PilotResult, EulerZYX_t *EulerAngles, EulerRates_t *EulerRates, float altitude, float *motors)
{
	if (PilotResult->throttlePercentage < MAX_VALUE_NO_PROP_SPIN)
	{
		for (int i = 0; i < 4; i++)
		{
			motors[i] = MOTOR_VALUE_NO_SPIN;
		}

		altitudeAccumulatedIntegral = 0.0f;
		xAccumulatedIntegral = 0.0f;
		yAccumulatedIntegral = 0.0f;
		zAccumulatedIntegral = 0.0f;

        softStartMotorPercent = 0.0f;

        inFLight = false;

		return AAQUAD_SUCCEEDED;
	}

    float targetXAngle = MAX_X_THROW * (PilotResult->xPercentage / 100.0f);
    float targetYAngle = MAX_Y_THROW * (PilotResult->yPercentage / 100.0f);
    float targetZAngle = MAX_Z_THROW * (PilotResult->zPercentage / 100.0f);
    float targetAltitude = MAX_ALTITUDE * ((PilotResult->throttlePercentage - MAX_VALUE_NO_PROP_SPIN)/ 100.0f);	// TODO map the ranges instead

    float rollPercent = ComputeHeadingPid(targetXAngle, EulerAngles->phi, EulerRates->phiDot, kpX, kiX, kdX, &xAccumulatedIntegral);
    float pitchPercent = ComputeHeadingPid(targetYAngle, EulerAngles->theta, EulerRates->thetaDot, kpY, kiY, kdY, &yAccumulatedIntegral);

    float yawPercent = ComputeZPid(targetZAngle, EulerAngles->psi, EulerRates->psiDot);

    float altitudePercent = ComputeAltitudePid(targetAltitude, altitude, EulerAngles);

    motors[0] = altitudePercent;
    motors[1] = altitudePercent;
    motors[2] = altitudePercent;
    motors[3] = altitudePercent;

	motors[0] -= rollPercent;
	motors[1] -= rollPercent;
    motors[2] += rollPercent;
    motors[3] += rollPercent;

	motors[0] += pitchPercent;
    motors[1] -= pitchPercent;
	motors[2] += pitchPercent;
	motors[3] -= pitchPercent;

	motors[0] -= yawPercent;
    motors[1] += yawPercent;
    motors[2] += yawPercent;
	motors[3] -= yawPercent;

	ConstrainMotorRanges(motors);

	return AAQUAD_SUCCEEDED;
}

static float ComputeHeadingPid(float desired, float actual, float actualRate, float kp, float ki, float kd, float *accumulatedIntegral)
{
    float error = desired - actual;

    if (inFLight)   // accumulating the integral while on the ground would cause it to windup
    {
        *accumulatedIntegral += (TS * error);
    }

    return ((kp * error) + (ki * (*accumulatedIntegral)) - (kd * actualRate));
}

static float ComputeZPid(float desired, float actual, float actualRate)
{
    float error = desired - actual;

    if (error > (float) M_PI)
    {
        error = (desired - actual) - (2.0f * (float) M_PI);
    }
    else if (error < ((float) -M_PI))
    {
        error = (2.0f * (float) M_PI) + desired - actual;
    }

    if (inFLight) // accumulating the integral while on the ground would cause it to windup
    {
        zAccumulatedIntegral += (TS * error);
    }

    return ((kpZ * error) + (kiZ * (zAccumulatedIntegral)) - (kdZ * actualRate));
}

static float ComputeAltitudePid(float desired, float actual, EulerZYX_t *EulerAngles)
{
	// TODO: In the future, you should be dividing the altitudeHoldValue by the euler angles to ensure enough thrust to keep the aircraft at the right height.
	(void) EulerAngles;

    static float motorPercentLevelAltitudeHold;
    static bool newDataHasArrived;

    if ( ! inFLight )
    {
        if (actual > 0.03f)
        {
            inFLight = true;

            motorPercentLevelAltitudeHold = softStartMotorPercent;

            for (int i = 0; i < 3; i++)
            {
                historicalAltitudeValue[i] = actual;
            }

            softStartMotorPercent = 0.0f;
        }

        softStartMotorPercent += 10.0f * TS;

        return softStartMotorPercent;
    }

    if ( ! isnan(actual) ) // altitude refresh is slower than control loop, so only update result when new data comes in.
    {
        historicalAltitudeValue[2] = historicalAltitudeValue[1];
        historicalAltitudeValue[1] = historicalAltitudeValue[0];
        historicalAltitudeValue[0] = actual;

        newDataHasArrived = true;
    }

    float error = desired - historicalAltitudeValue[0];
    float altitudeHoldValue = motorPercentLevelAltitudeHold;

    float derivative = ((3 * historicalAltitudeValue[0]) - (4 * historicalAltitudeValue[1]) + (historicalAltitudeValue[2])) / TSA;

    if (newDataHasArrived)
    {
        altitudeAccumulatedIntegral += (TSA * error);
    }

    newDataHasArrived = false;

    return (altitudeHoldValue + (kpA * error) + (kiA * altitudeAccumulatedIntegral) - (kdA * derivative));
}

static void ConstrainMotorRanges(float *motors)
{
    for(int i = 0; i < 4; i++)
    {
        if (motors[i] > 99.0f)
        {
            motors[i] = 99.0f;
        }
        else if (motors[i] < MOTOR_VALUE_NO_SPIN)
        {
            motors[i] = MOTOR_VALUE_NO_SPIN;
        }
    }
}

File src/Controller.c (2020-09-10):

#include "Controller.h"
#include "PilotInstructions.h"
#include "Imu.h"
#include "Altitude.h"
#include "MahonyAHRS.h"
#include "Pid.h"
#include "PwmChip.h"
#include "Leds.h"

#include "Common.h"

#include <avr/interrupt.h>

/***********************************************************************************************************************
 * Definitions
 **********************************************************************************************************************/

typedef enum state
{
	CTRL_GET_PILOT_INSTRUCTIONS,
	CTRL_GET_IMU_DATA,
    CTRL_GET_ALTITUDE,
    CTRL_TRIGGER_NEW_MEASUREMENTS,
    CTRL_FUSE_MEASUREMENTS,
    CTRL_CONVERT_TO_EULER,
	CTRL_COMPUTE_PID,
	CTRL_SEND_TO_PWM,
	CTRL_WAIT_FOR_TIMER,
	CTRL_FAILED

}Controller_State_t;

#define TIMER_VAL_1_PERIOD ((uint16_t) ((float) CTRL_LOOP_PERIOD / (8.0f / (float)F_CPU)))   // assuming clk divider of 8.

#define DANGER_ANGLE 1.3f   // radians

/***********************************************************************************************************************
 * Variables
 **********************************************************************************************************************/

static Controller_State_t currentState;

static PilotResult_t PilotResult;
static ImuData_t ImuData;
static float altitude;
static EulerZYX_t EulerAngles;
static EulerRates_t EulerRates;
static float motors[4];

static bool periodHasPassed;

/***********************************************************************************************************************
 * Prototypes
 **********************************************************************************************************************/

static Controller_State_t GetPilotInstructions_State(void);
static Controller_State_t GetImuData_State(void);
static Controller_State_t GetAltitude_State(void);
static Controller_State_t TriggerNewMeasurements_State(void);
static Controller_State_t FuseMeasurements_State(void);
static Controller_State_t ConvertToEuler_State(void);
static Controller_State_t ComputePidState(void);
static Controller_State_t SendToPwm_State(void);
static Controller_State_t WaitForTimer_State(void);
static Controller_State_t Failed_State(void);

static void InitData(void);
static void InitPeriodTimer(void);

/***********************************************************************************************************************
 * Code
 **********************************************************************************************************************/

void Controller_Init(void)
{
    sei();  // global interrupt enable
	PilotInstructions_Init();
    Imu_Init();
    Altitude_Init();
    Pid_Init();
	PwmChip_Init();
    Leds_Init();

    InitData();
    InitPeriodTimer();

	currentState = CTRL_TRIGGER_NEW_MEASUREMENTS;
}

void Controller_DoYourThingAndFlyTheQuadITrustYou(void)
{
	Controller_State_t nextState;
	switch(currentState)
	{
		case CTRL_GET_PILOT_INSTRUCTIONS:
			nextState = GetPilotInstructions_State();
			break;

		case CTRL_GET_IMU_DATA:
			nextState = GetImuData_State();
			break;

        case CTRL_GET_ALTITUDE:
            nextState = GetAltitude_State();
            break;

        case CTRL_TRIGGER_NEW_MEASUREMENTS:
            nextState = TriggerNewMeasurements_State();
            break;

        case CTRL_FUSE_MEASUREMENTS:
            nextState = FuseMeasurements_State();
            break;

        case CTRL_CONVERT_TO_EULER:
            nextState = ConvertToEuler_State();
            break;

		case CTRL_SEND_TO_PWM:
			nextState = SendToPwm_State();
			break;

        case CTRL_COMPUTE_PID:
            nextState = ComputePidState();
            break;

        case CTRL_WAIT_FOR_TIMER:
            nextState = WaitForTimer_State();
            break;

        case CTRL_FAILED:
            nextState = Failed_State();
            break;

		default:
			nextState = CTRL_FAILED;
			break;
	}

	currentState = nextState;
}

static void InitData(void)
{
    // All this initial data represents a quadcopter that's on
    // level ground, not moving and pointing in some arbitrary direction.
    PilotResult.xPercentage = 0.0f;
    PilotResult.yPercentage = 0.0f;
    PilotResult.zPercentage = 0.0f;
    PilotResult.throttlePercentage = 0.0f;

    ImuData.gyrX = 0.0f;
    ImuData.gyrY = 0.0f;
    ImuData.gyrZ = 0.0f;
    ImuData.accX = 0.0f;
    ImuData.accY = 0.0f;
    ImuData.accZ = 1.0f;
    ImuData.magX = 1.0f;
    ImuData.magY = 0.0f;
    ImuData.magZ = 0.0f;

    altitude = 0.0f;
}

static void InitPeriodTimer(void)
{
    TIMSK4 = (1 << OCIE4A); // interrupt on match
    OCR4A = TIMER_VAL_1_PERIOD;
    TCCR4B = (1 << CS41); // clk divided by 8
}

static Controller_State_t GetPilotInstructions_State(void)
{
    static int numCallsSinceSuccess;
    int nextState;

	int r = PilotInstructions_ComputePilotResult(&PilotResult);

    switch(r)
    {
        case AAQUAD_SUCCEEDED:
        {
            numCallsSinceSuccess = 0;
            nextState = CTRL_GET_IMU_DATA;
            break;
        }

        case AAQUAD_BUSY:
        {
            numCallsSinceSuccess ++;

            int missedComWindows = (CTRL_LOOP_PERIOD / PILOT_INSTRUCTIONS_REFRESH_PERIOD) * numCallsSinceSuccess;

            if (missedComWindows >= 3)  // we've lost communication with the transmitter
            {
                nextState = CTRL_FAILED;
            }
            else
            {
                nextState = CTRL_GET_IMU_DATA;
            }
			break;
        }

        case AAQUAD_FAILED:
        {
            nextState = CTRL_FAILED;
            break;
        }

        default:
        {
            nextState = CTRL_FAILED;
            break;
        }
    }


	return nextState;
}

static Controller_State_t GetImuData_State(void)
{

	int r = Imu_GetResult(&ImuData);

    if(r == AAQUAD_FAILED)
    {
        return CTRL_FAILED;
    }

    return CTRL_GET_ALTITUDE;
}

static Controller_State_t GetAltitude_State(void)
{

    int r = Altitude_Get(&altitude);

    if (r == AAQUAD_FAILED)
    {
        return CTRL_FAILED;
    }

    else if (r == AAQUAD_BUSY)
    {
        // This way, PID will know no new data is available.
        altitude = NAN;
    }

    return CTRL_TRIGGER_NEW_MEASUREMENTS;
}

static Controller_State_t TriggerNewMeasurements_State(void)
{
    Altitude_BeginMeasurement();
    Imu_BeginRead();

    return CTRL_FUSE_MEASUREMENTS;
}

static Controller_State_t FuseMeasurements_State(void)
{
    // this module makes the return data available as the global variables q0, q1, q2 and q3
    MahonyAHRSupdateIMU(ImuData.gyrX, ImuData.gyrY, ImuData.gyrZ, ImuData.accX, ImuData.accY, ImuData.accZ);

    return CTRL_CONVERT_TO_EULER;
}
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

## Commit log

2019-03-05 completed phase 1 of the pilot instructions module and began work on the I2CDriver and the pwmChip modules
2019-03-09 Completed phase 1 --All 4 motors smoothly controlled in unison via flight computer
2019-03-10 phase 2 of developement complete --all 4 receiver channels incorporated allowing control of 3 degrees of freedom and throttle
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2019-03-20 Added a periodic Sensor Reset and Complementary filter bug fixes
    [Controller.c, Pid.c]
2019-03-21 Completed the complementary filter, began i,plementing the pd functionality of the pid module
2019-03-25 Completed a physical Analysis of the AAQuad and used the results to build a tesing framework that was used to tune the PID
    [rawData.csv]
2019-04-13 Fixing tesyt runners for Pid ad Low pass filter to correspond to observed results
    [FlatTest-MovingAverage.csv, flatTest.csv]
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2019-05-01 critical damping achieved, digital lowpass filter no longer necessary, gyro settings altered to filterin hardware
2019-05-02 added PID for the yaw axis and tuned the calibration module as well as the PID coefficients in accordance with a 3D test
2019-05-08 removed LowPassFilterTests folder. Sufficient filtering was already found to have been done by the gyroscope and the lowPassFilter module was since removed.
    [FlatTest-MovingAverage.csv, flatTest.csv]
2019-05-08 added KiCad and schematic files
    [AAquad_PCB-2019-05-08-17-19-43.sch, AAquad_PCB-2019-05-08-17-33-20.sch, AAquad_PCB.kicad_pcb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]
2019-05-15 forced motors to 0 at startup
    [AAquad_PCB.kicad_pcb]
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2019-05-20 Calibration mode working and tested, fixed unit tests, and updated readme
    [Controller.c]
2019-05-20 Moved a macro useful to Calibration into common.h and fixed README typos
    [Pid.c]
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2019-08-23 PCB redesign to include IMU, barometer, and various other features
    [AAquad_PCB.kicad_pcb, AAquad_PCB.sch]
2019-08-24 Completed PCB redesign
    [AAquad_PCB.kicad_pcb, AAquad_PCB.sch]
2019-08-24 Finished PCB Review. Sent out gerbers for manufacturing
    [AAquad_PCB-B_Cu.gbr, AAquad_PCB-B_Mask.gbr, AAquad_PCB-B_SilkS.gbr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]
2019-12-29 Updated Kicad Files and layout PDFs
    [BOM.csv]
2019-12-29 Designed the pid controller in simulink
    I've replaced the custom built C module "PidTests" with a simulink model
    I've designed to use the 6 dof block to properly model the quadcopter.
    The closed loop control structure that deals with processing the euler
    angles and executing the appropriate pid algorithms have also been
    implemented.
    At this time, I've set up the model to output a crude simulation result
    that tracks the velocity, angular velocity, displacement and angular
    position of the quadcopter.
    Note that the values used in the model describing quadcopter parameters
    such as weight, thrust, torque... have not been adjusted to deal with
    the new frame.
    [rawData.csv]
2020-01-04 Created the driver for the new IMU chip.
    Wrote and successfully tested an interrupt based SPI driver for the
    bmx160. The driver initialises the chip and allows collection of the
    accelerometer, gyroscope and magnetometer data.
    On top of this, the processor clock has been sped up to 20MHz and the
    spi clock runs at 10 MHz.
    Although the driver has been tested, it is not yet integrated with the
    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
2020-01-12 Made the pwmchip I2C driver interrupt based
    There are now no blocking calls associated with the pwm chip. The I2C
    driver runs at 100 KHz.
    Although the driver has been tested and functions, it is not yet
    integrated with the rest of the code. With this commit, the code will
    still compile, but will not fly a quadcopter properly until changes are
    made to the controller module.
2020-01-18 Deleted polling I2C drivers
    These have now been replaced by their interrupt based equivalents. All
    modules relying on I2C (IMU and PWMCHIP) have been modified to work with
    the new drivers.
2020-01-18 Developed a driver for the ultrasonic distance sensor
    The flight computer can now use altitude data from the ultrasonic
    distance sensor via the Altitude module. No calls to this module are
    polling based.
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2020-01-21 Renamed "Schematics" directory to "PCB" and added some pictures of the newest PCB.
    [AAquad_PCB-2019-05-08-17-19-43.sch, AAquad_PCB-2019-05-08-17-33-20.sch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]
2020-02-01 Altitude module now uses 16 bit timer to measure the echo pulse
    Previous to this, an 8 bit timer was used. However, it was overflowing
    many times for longer echo pulses. A 16 bit timer ensures that there
    will never be more than 1 timer overflow during the longest possible
    echo pulse.
2020-02-02 Removed the obsolete SensorData module
    Now that the drivers for the IMU and altitude sensor have been completed
    and tested, it is fine to delete the SensorData module, which was
    responsible for reading various sensors on the previous iteration of
    the PCB. Not only were the sensors different, making it useless, but
    the SensorData module relied on polling, making the decision to
    deprecate it more reasonable than a decision to update it.
2020-02-02 Flipped boolean "isFallingEdge" flag with logical not instead of XOR
    It is safer to use logical operations rather than bitwise ones on
    boolean values.
    [Altitude.c]
2020-04-22 Centralized the interrupt functionality relevant to the Pilot instructions module inside it.
    Previous to this change, the external interrupts responsible for reading
    the pwm signals coming from the receiver were initialized in main and
    the ISRs existed in "interrupts.c". With this change, The
    PilotInstructions module takes care of initializing its interrupts and
    holds the ISRs, thus removing the need for an interrupt module and
    cleaning up main.
2020-04-25 Imu_get_result now returns gyro data in rad/s
    Previous to this, gyro units were arbitrary. Magnetometer and
    accelerometer data remain in arbitrary units, as those vectors are
    normalized. This is reflected in the function's description.
2020-04-25 Changed documentation of PilotInstructions_ComputePilotResult to reflect that the return struct is only modified in the case of success.
2020-04-26 Made variables responsible for reading data from timers volatile.
    I detected some intermittent problems with the PilotInstructions and
    Altitude modules when various compiler optimization settings were
    tested. Making the relevant variables volatile seemed to fix the issues.
    [Altitude.c, PilotInstructions.c]
2020-04-26 Integrated multiple modules into Controller to add functionality up to gathering and fusing all data from the sensors.
    This is a large and important commit. As of this commit, Controller's
    state machine reflects the design from the flowchart and can effectively
    collect Pilot instructions, altitude, and IMU data from the relevant
    hardware. This is all done in a real time loop (20ms period at the
    moment).
    The other new change is the introduction of the MahonyAHRS module, which
    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
2020-04-28 Tuned the matlab model PID
    Found all the relevant coefficients such that, given simple commands, the model obeys the requested instructions without too much overshoot.
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2020-04-29 Fixed important bug in Altitude.c
    Previous to this change, the echo pulse of the ultrasonic distance
    sensor would only be properly measured if it represented an altitude
    below 50 cm and if the timer that measured it did not wrap around.
    With this change, the timer that measures the echo pulse has been
    prescaled by a factor of 64, so all altitudes in the sensor's range can
    be measured. Also, the edge case of the timer overflowing during the
    measurement has been covered and tested.
    [Altitude.c]
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2020-04-30 Swapped the x and y axis in the Pilot instructions module
    I found out that the PilotInstructions module refered to roll as "y" and
    pitch as "x". This is backwards in the reference system I chose and am
    using in the Pid module so I swapped them in the Pilot Instructions
    module.
    [PilotInstructions.c]
2020-04-30 Increased control loop frequency from 50 to 200 Hz
    Doing some testing, it was observed that it takes roughly 3 ms for all
    the math to be done in a single control loop iteration. Since the Imu
    supports 200 Hz gyro and acc data rates, it is certainly possible to
    output results at this speed.
    Although it was not extensively tested, increasing the control loop
    frequency can only be beneficial, as finer corrections can be made more
    often, resulting in smoother and more stable characteristics.
    The Imu driver had to be modified to increase the gyroscope and
    accelerometer ODRs so as to support the increased data rate. The Mahony
    filter was updated with the new control loop frequency, as was the ma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
    [Altitude.c, Controller.c, Imu.c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]
2020-04-30 Fixed typo in a macro used to config the IMU
    The macro ACC_ODR_800_OSR4 was used to config the gyro rather than the
    correct GYRO_ODR_800_OSR4. They both happened to evaluate to the same
    value, so this change will not affect actual performance in any way.
    [Imu.c]
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2020-05-03 Reduced the value associated with MOTOR_VALUE_NO_SPIN
    The old value was slightly too high, so the motors sometimes refused to start (there is a safety mechanism in the esc that does not allow the motors to start spinning unless a state of near 0 throttle is entered first). With the new value of 0.5, this problem has not been detected.
2020-05-03 Completed the calibration sequence of the magnetometer and gyroscope
    As of this commit, there is a sequence of commands (that will be explained in the readme) that the pilot can use on startup to calibrate the magnetometer and gyroscope. The magnetometer calibration has effectively been shown to eliminate the hard iron biases present on the quad, which allows the sensor fusion algorithms to properly get the information about earth's magnetic field. The gyro calibration has also been effectively shown to eliminate the systematic error associated with the sensor.
    Aside from the above changes, the Calibration module now, once again, leverages the Leds to indicate to the pilot what stage of Cal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
    [Controller.c, Imu.c, Leds.c]
2020-05-04 Updated the Pid module with the latest gains and covered yaw edge case
    A few commits ago, the control loop was sped up to 200 Hz. As a result, the matlab model was updated and the optimal gains changed. Those latest gains are now reflected in the Pid module.
    Furthermore, it was discovered that there are possible discontinuities in the way the Pid algorithms treated the z axis. For example, if the pilot commanded -170 degrees while the quad was at 175 degrees, the old algorithm would attempt to "go around the long way". Such cases are now accounted for. I'll not that such cases are not possible in the x or y axes because the quad should never be close to "flipping around" anyway.
    [Pid.c]
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2020-05-09 Added safety functionality to disable the output in case of failure.
    With this commit, if the controller state machine ends up in the failed
    state for any reason, the PwmChip is instructed to turn off all its
    outputs, which in turn means the motors stop spinning.
    The solution is immune to a communication failure with the PwmChip
    aswell.
    [Controller.c, PwmChip.c]
2020-08-10 A lot of little things here. There is now a takeoff sequence, pilot gains were increased, we use error squared proportional control, and the matlab model was updated accordingly. Things work in that 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
    [Imu.c, Pid.c]
2020-08-10 Used the ZYX euler angles rather than the original XYZ
    Through some experimentation, it was discovered that if there was a non
    negligible amount of yaw, roll and pitch would become coupled with the
    XYZ sequence. This problem is not present in the ZYX sequence. In that
    case the coupling would be between yaw and pitch when roll was large.
    However, that is not an issue because unlike yaw, which can routinely
    take on practically any angular value, the roll and pitch angles will
    always be, by design, very small so as to keep the aircraft stable.
    [Controller.c, Pid.c]
2020-08-10 Used non magnetometer API of Mahony rather than full version
    I discovered that I live so far north that the earth's magnetic field around here is not actually perpendicular to gravity. This really confused the Mahony algorithm. In the future, I will make some software to correct the magnetometer readings for this, but for the time being, I'm moving forward without accounting for Earth's magnetic field.
    [Controller.c]
2020-08-11 Added initialisation delays
    There was a bug plaging this project for many weeks. It was eventually
    understood to be caused by a failure to properly initialize the
    accelerometer, which seems to be a result of not giving the SPI module
    enough time to initialise before putting it in use. This problem was
    solved by adding a delay to allow that time. A delay was also added to
    the very first line of the main function, for good measure.
    [SPI.c, main.c]
2020-08-11 More little things in this commit
    I've disabled the finding of the initial azimuth in the calibration since the
    magnetometer is not currently being used in the sensor fusion algorithm.
    I've also fixed the signs of the roll pitch and yaw adjustements in the pid
    module so they would correspond with reality. I also decided to go back to
    proportional control (rather than proportional squared) because results seem
    fine with it and I don't want to complicate things.
    I've fixed the calculation of the euler angle derivatives to correspond with
    the new Z,Y,X sequence.
    The change in the project file is there because I've removed the
    double-promotion warning. That was done because it turns out that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
    [Pid.c]
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2020-08-23 final commit before release
    The big change in this commit is the addition of a lowPass filter to
    smooth altitude data as it was found to contain outliers that threw off
    the derivative wildly.
    The other major change is a further optimization of the pid gains. The
    new gains were found by the matlab model to give better results.
    All other changes are typos that were fixed and comments that were
    added.
    The Readme was modified to reflect the current state of the project.
    [Altitude.c, Controller.c, Pid.c]
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2020-09-10 Added safety functionality to detect transmitter failure
    [Controller.c]
2020-09-10 Failed state now attempts an active shutdown before turning off the output
    [Controller.c]
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
